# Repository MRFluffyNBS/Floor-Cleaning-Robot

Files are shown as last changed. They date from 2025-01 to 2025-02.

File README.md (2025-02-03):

# Floor-Cleaning-Robot (***Work in Progess***)
This is my attempt during winter break this year at making a (knockoff) Roomba aka a floor-cleaning robot. I wanted to work on a rather simple project over winter break and the topic of a robot vacuum came up when one of my friends suggested the idea. Honestly, I feel like a lot of people have done this before so I primarily did this project just to gain some experience/knowledge. Please keep in mind that this is still a very rough build and there is a lot of stuff I could improve on for this project and also a lot of stuff that I still want to do. I can elaborate on this later, but basically it would have been way better if I actually could get reliable access to a 3d printer... 
As you can see in the following picture of the roomba (I'll be calling it that from now on), a lot of it is being held on with cardboard and tape. 

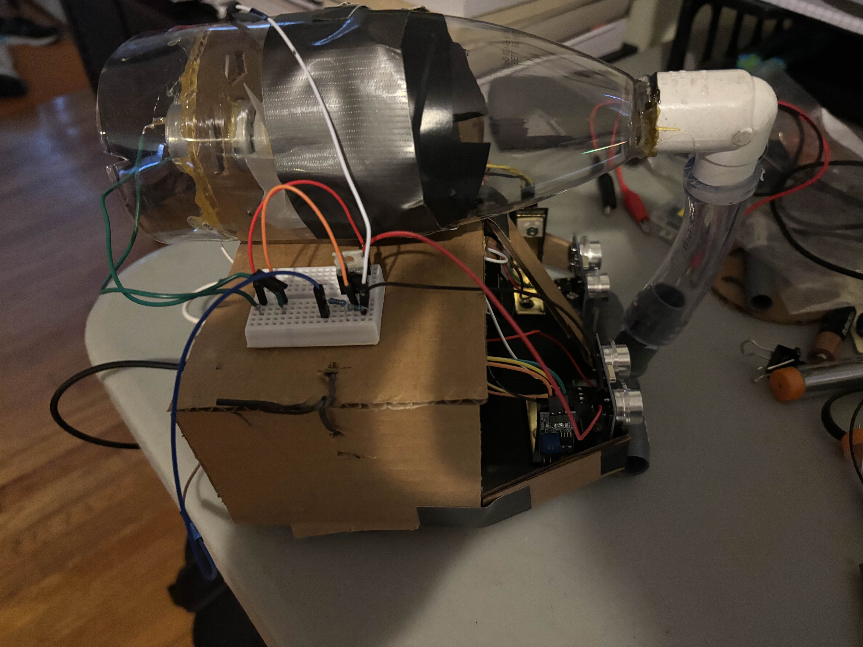
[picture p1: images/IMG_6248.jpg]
Image of completed roomba


### Video demo: 
Iroomba video demo (http://www.youtube.com/watch?v=Y5IRyU6TOsk)

***Click the image above to play video***

Even though the construction may not be the sturdiest, the "roomba" runs well most of the time and is pretty good at obstacle avoidance given that there isn't a carpet or high beam for the robot to get caught on. Once I can use a 3d printer more often, the next goal would be to construct a sleeker and shorter chassis much like a real roomba so that the robot can move around easier. However, the base plate and wheels of the robot are 3d printed, however, there are also parts of the design that I would like to improve on seeing that I could only get stuff 3d printed once at my library. I have also included the CAD files in the repo. Hopefully in the future I can actually get access to a 3D printer :C

## Overview

The microcontroller I am using is an esp32 chip mounted on an Adafruit feather Huzzah32. A normal Arduino uno or most other microcontrollers can be used as well I just used the esp32 because of its wifi features because I also want to implement some web server functionality in the future as well (such as remote control options and updating on status). The motor driver I'm using is a DRV8833 motor driver with two H bridges. It can supply up to 1.5A and I am using two n20 motors geared at about 200 rpm to drive the Roomba wheels. The motor for the vacuum is an RS360 motor and I am just powering that with 6 AA batteries and a MOSFET to turn the vacuum on/off. I am using two HC-SR04 ultrasonic sensors to detect obstacles and two ir proximity sensors to detect if there is a fall off (e.g. the edge of stairs or a table). 

adafruit feather
Adafruit Feather Huzzah ESP32

## Step 1: Chassis + wheels
<p float="left">
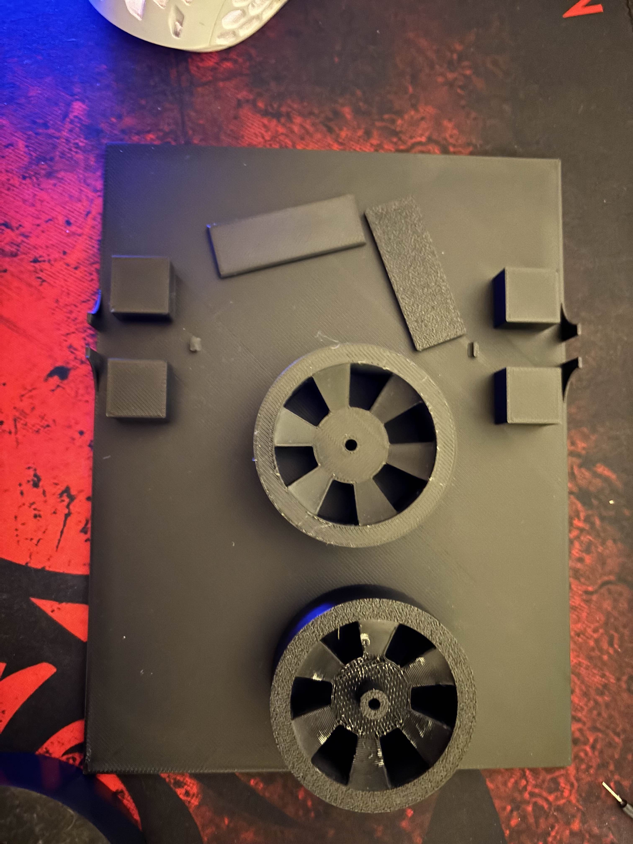
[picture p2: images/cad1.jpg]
Chassis 1
   
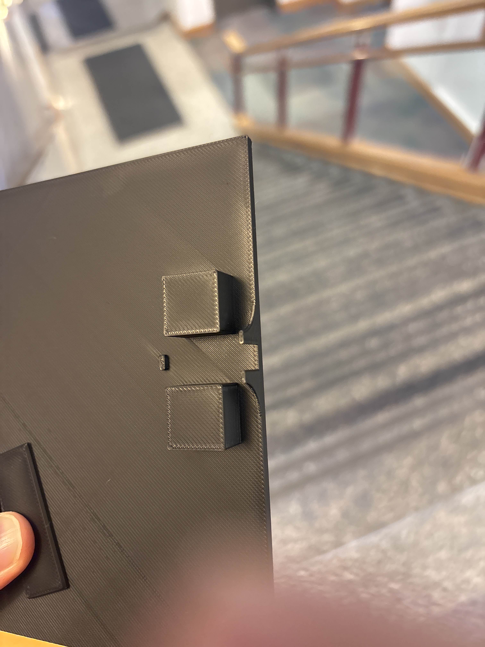
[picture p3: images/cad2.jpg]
Chassis 2
  
</p>

## Step 2: Motor driver + Motors
Chassis 2
In order to control the motor driver, you have to use a H bridge that allows for motors to be run both forward and backward. A H bridge consists of basically 4 transistors. The transistors or switches alternate between npn and pnp resistors, so when a HIGH signal is applied to one side, it turns a switch on and the other switch off. This prevents short circuits and means you only need two inputs to control a h bridge. The motor driver I used had two H bridges so it could control two motors. For each pair of inputs, I connected two GPIO pins on the ESP32. These inputs corresponded to the two wires leading to the motors. To turn the motors on in either direction you just need to set one input pin to HIGH and the other one to LOW. In order to control speed, I made sure all GPIO pins supported PWM. Just use PWM on the input that is normally set HIGH to control the motor speed. 

## Step 3: Sensors 
Sensors intial
For sensors, I used two ultrasonic sensors on the front end of the roomba. If a sensor detects an object in front of it, the roomba turns a random angle the other direction. The same logic is applied to the IR sensors but instead, they are there to make sure there is always a solid floor beneath. The ultrasonic sensor works by sending out a pulse that bounces off an object and is then read by the sensor. The code for this is fairly simple and can be easily found online. Just make sure to account for a 0 in the reading because sometimes the sensor times out and doesn't output a valid reading. This could erroneously trigger that an object is detected in front. 

## Step 2: Motor and Sensor Libraries 
To make writing code easier and allow for better integration of the software when writing a pathfinding algorithm/future setting up for remote use, I made separate classes for turning the motors and object detection for both the ultrasonic sensors and IR proximity sensors. Using these classes, I could create simple functions such as forward/reverse to move the Roomba and also one single command to check if there is an object in front of the sensors. I wrote these classes a separate file in the format of Arduino libraries. They are split into two files each with a .h file for method/class prototypes and a .cpp file for the actual implementation. This [video](https://www.youtube.com/watch?v=IiZl3p-ZohM) goes into it in more detail. 

## Step 5: Powering the Roomba 
Initially I was powering the board, sensors and motors from one LiPo battery. I switched that to a small portable usb charger but there were still problems. One of the biggest problems I had when getting the Roomba to work was the unreliability of the sensors when the motors were under load. When the robot was moving under its own weight, many times it would run into a wall without the sensors triggering. After testing through the serial monitor, I realized that the motors might have been causing a bunch of noise in the system when under load because it would need to draw more power from my power source. After doing some research, I realized that motors were very prone to causing electrical noise and thus needed either capacitors to smooth the voltage or be run off a separate power source. I decided to use a separate power source because it seemed simpler to do so and also because I realized drawing power from two separate usb outputs on the portable charger basically mimicked two separate power sources. As long as you connect the grounds together, the digital logic of the microcontroller will be able to control the motors. 

## Step 6: Vacuum 
For the vacuum, instead of a 5v usb charger, I used 6 AA batteries that would provide 9 volts to the r360 dc motor. This motor draws about 0.8A and could probably be overclocked to 12 volts for a more powerfult vacuum. To turn the vacuum motor on/off, I used a MOSFET to create a relay that could be controlled by the microcontroller. The battery and motor would be connected through the source and drain pins with a 100k resistor between the gate and drain pins to prevent built-up charge in the transistor. A GPIO pin would be connected to the gate with the grounds of the microcontroller and transistor also tied together. In terms of the actual vacuum, I cut a circle of plastic into 8 slices and then used heat to help mold it into a crude fan. I then stuck it onto the motor and used a plastic bottle as the casing with a vegetable mesh between the fan blades and opening. Mostly, my designed was adapted off this [tutorial](https://www.instructables.com/How-to-Make-a-Powerful-Vacuum-Cleaner/). 

## Step 7: Putting everything together 
Sensors intial
Screws were used to mount L brackets and the IR sensors to the front. The ultrasonic sensors also came with screw-mounted brackets. The motors were screwed on with the 3d printed fittings and I also added electrical tape to the wheels for better traction. The breadboard with the esp32 and motor driver were taped on top of the portable charger bank which was then mounted on the back of the roomba. Also I glued the hump piece to the front underside of the roomba so it would stand level. Make sure that most of the weight is right above the wheel axles and not the front hump or else there will be too much friction. Lastly, since I didn't have the time and also the means of using a 3d printer, I just used plain cardboard to create a mount that would hold the vacuum bottle in place along with its relay circuit. In the future, I would like to create a better 3d printed bracket that is not so bulky and also 3d print a better casing for the vacuum. Lastly, I coded in a while loop that would trigger until a button was pressed so that the roomba wouldn't automatically start until I wanted it to. 

## Extra + TODO: Wireless Controlling with ESP32
In the future, other than making a more sleek and compact build that is more 3d printed than cardboard, I also want to integrate the esp32 wifi feature into my project. Right now, I have a remote test folder that contains code that allows me to control the roomba like a rc car. Im hoping to be able to have the roomba give updates onto a html webserver and be able to have a toggle for manual control and automatic control. I always want to be able to turn on and off the vacuum motor itself remotely. Right now, I need to figure out a way to upload the html code onto the webserver in a way where there isnt any lag or any sort of delay because during testing I found that there was often a delay between pressing a button on the website and the roomba actually moving.

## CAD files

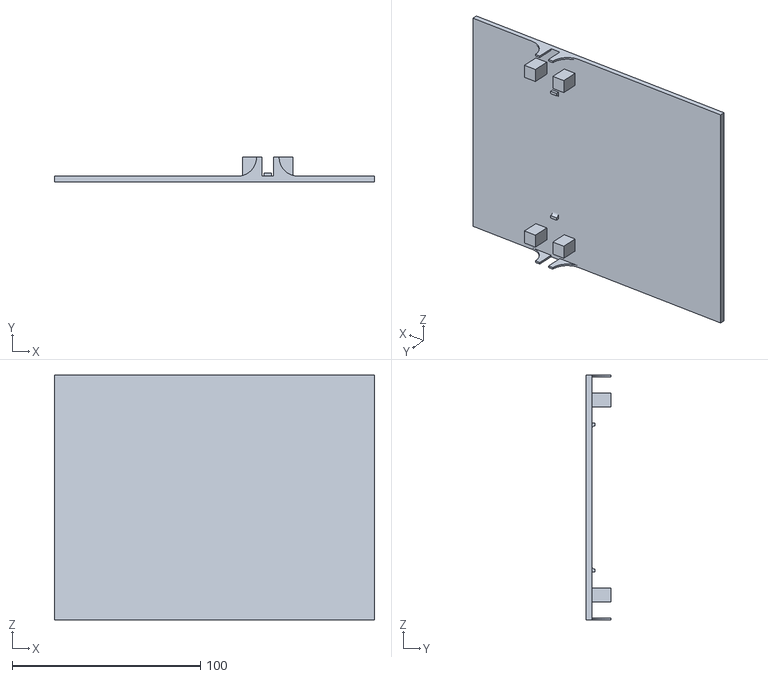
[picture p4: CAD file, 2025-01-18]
baseplate3.STL
170.0 x 13.1 x 130.0

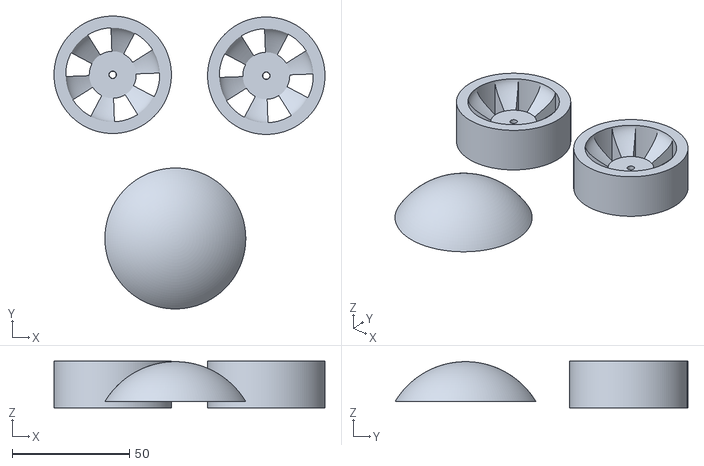
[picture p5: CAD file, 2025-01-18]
wheel+front hump.stl
115.4 x 124.7 x 20.0

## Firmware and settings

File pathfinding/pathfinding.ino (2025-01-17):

#include "roomba_motors.h"
#include "sensors.h"

//right motor pin1 and pin2
const int motor_pin1 = 16;
const int motor_pin2 = 17;
//left motor pin3 and pin4 
const int motor_pin3 = 27;
const int motor_pin4 = 33; 
//duration and speed settings
const int duration = -1; //set the duration to -1 for the motors to turn continously until method stop() is called
int speed = 150;
//Motors initalize
Motors roomba(motor_pin1, motor_pin2, motor_pin3, motor_pin4, speed);

const int rtrig_pin = 18;
const int recho_pin = 5;

const int ltrig_pin = 32;
const int lecho_pin = 15;

const int sensor_tolerance = 15;

Ultson rightSonic(rtrig_pin, recho_pin, sensor_tolerance);
Ultson leftSonic(ltrig_pin, lecho_pin, sensor_tolerance);

const int rir_pin = 4;
const int lir_pin = 14; 

Irsensor rIr(rir_pin);
Irsensor lIr(lir_pin);

const int button_pin = 19;

int degrees = 90;
int direction = 0;

const int switch_pin = 12;

void setup() {
  // put your setup code here, to run once:
  Serial.begin(115200);
  //set pimode for motors
  roomba.begin();
  roomba.printMotors();
  //set pinmode for the ultrasonic sensors
  rightSonic.begin();
  leftSonic.begin();

  rIr.begin();
  lIr.begin();
  
  pinMode(button_pin, INPUT);
  pinMode(13, OUTPUT);
  //set random seed to arbitrary number 
  randomSeed(12346);
  //setting up pinmode for GPIO pin that switches on/off the vacuum
  pinMode(switch_pin, OUTPUT);
  digitalWrite(switch_pin, LOW); //ensures the vacuum is turned off before the roomba starts working
  Serial.println("Off, waiting for signal...");

  while (digitalRead(button_pin) == LOW) { //waits for button to be pressed to turn on
  }

  Serial.println(" Turning on...");
  digitalWrite(switch_pin, HIGH); //turn on high (temp)
}

void loop() {
  //check if the right ultrasonic sensor detects an object first
  
  if (rightSonic.objectDetected() == true || rIr.checkDistance() == true) {
    Serial.println("Right sensor detected");
    roomba.stop();
    delay(100);//Gives the motors time to wind down 
    //Somtimes the only one motor spins up when going directly into reverse
    roomba.reverse(800);

    roomba.stop();
    degrees = random(45, 136); // random number from 45 to 135 degrees
    float time = degrees * (400.0 / roomba.getSpeed());
    //Serial.print("Degrees/time of rotation: "); 
    //Serial.println(time);
    //Turns opposite direction to which sensor has detected an object
    //most likely there is more space on the left if the right sensor detects somehting first
    roomba.left(time);
    delay(60);
    roomba.forward();
  }
  else if (leftSonic.objectDetected() == true || lIr.checkDistance() == true) {
    Serial.println("Left sensor detected");
    roomba.stop();
    delay(100); //Gives the motors time to wind down 
    //Somtimes the only one motor spins up when going directly into reverse
    roomba.reverse(800);

    roomba.stop();
    degrees = random(60, 181); // random number from 45 to 180 degrees
    float time = degrees * 5.0;
    //Serial.print("Degrees/time of rotation: "); 
    //Serial.println(time);
    //same reteoric as the other sensor
    roomba.right(time);
    delay(60);
    roomba.forward();
  }
    else {//proceed forward
    //delay(60);
    roomba.forward();
    }
}

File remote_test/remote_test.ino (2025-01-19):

/*
Testing for remote controlling a car through wifi. Adapted from code from a tutorial from randomnerdtutorials.com
Nathaniel Su 1/4/2025


// Load Wi-Fi library
#include <WiFi.h>
#include "roomba_motors.h"
#include <WebServer.h>

//right motor pin1 and pin2
const int motor_pin1 = 16;
const int motor_pin2 = 17;
//left motor pin3 and pin4 
const int motor_pin3 = 27;
const int motor_pin4 = 33; 
//duration and speed settings
const int duration = -1; //set the duration to -1 for the motors to turn continously until method stop() is called
int speed = 255;
//Motors initalize
Motors roomba(motor_pin1, motor_pin2, motor_pin3, motor_pin4, speed);

// Replace with your network credentials
const char* ssid = "Feather-esp32-Roomba";
const char* password = "123456789";

// Set web server port number to 80
WiFiServer server(80);

// Variable to store the HTTP request
String header;

// Auxiliar variables to store the current output state
String output26State = "off";
String output27State = "off";

// Current time
unsigned long currentTime = millis();
// Previous time
unsigned long previousTime = 0; 
// Define timeout time in milliseconds (example: 2000ms = 2s)
const long timeoutTime = 2000;

void setup() {
  Serial.begin(115200);
  //Initialize motors first 
  roomba.begin();
  roomba.printMotors();

  // Connect to Wi-Fi network with SSID and password
   // Connect to Wi-Fi network with SSID and password
  Serial.println("Setting AP (Access Point)…");
  // Remove the password parameter, if you want the AP (Access Point) to be open
  WiFi.softAP(ssid, password);

  IPAddress IP = WiFi.softAPIP();
  Serial.print("AP IP address: ");
  Serial.println(IP);
  
  server.begin();
}

void loop(){
  WiFiClient client = server.available();   // Listen for incoming clients

  if (client) {                             // If a new client connects,
    currentTime = millis();
    previousTime = currentTime;

    Serial.println("New Client.");          // print a message out in the serial port
    String currentLine = "";                // make a String to hold incoming data from the client
    while (client.connected() && currentTime - previousTime <= timeoutTime) {  // loop while the client's connected
      currentTime = millis();
      if (client.available()) {             // if there's bytes to read from the client,
        char c = client.read();             // read a byte, then
        Serial.write(c);                    // print it out the serial monitor
        header += c;
        if (c == '\n') {                    // if the byte is a newline character
          // if the current line is blank, you got two newline characters in a row.
          // that's the end of the client HTTP request, so send a response:
          if (currentLine.length() == 0) {
            // HTTP headers always start with a response code (e.g. HTTP/1.1 200 OK)
            // and a content-type so the client knows what's coming, then a blank line:
            client.println("HTTP/1.1 200 OK");
            client.println("Content-type:text/html");
            client.println("Connection: close");
            client.println();
            
            // turns the GPIOs on and off
            if (header.indexOf("GET /26/on") >= 0) {
              Serial.println("GPIO 26 on");
              output26State = "on";
              roomba.forward();
            } 
            else if (header.indexOf("GET /26/off") >= 0) {
              Serial.println("GPIO 26 off");
              output26State = "off";
              roomba.stop();
            } 
            else if (header.indexOf("GET /27/on") >= 0) {
              Serial.println("GPIO 27 on");
              output27State = "on";
              roomba.reverse();
            } 
            else if (header.indexOf("GET /27/off") >= 0) {
              Serial.println("GPIO 27 off");
              output27State = "off";
              roomba.stop();
            }
            
            // Display the HTML web page
            client.println("<!DOCTYPE html><html>");
            client.println("<head><meta name=\"viewport\" content=\"width=device-width, initial-scale=1\">");
            client.println("<link rel=\"icon\" href=\"data:,\">");
            // CSS to style the on/off buttons 
            // Feel free to change the background-color and font-size attributes to fit your preferences
            client.println("<style>html { font-family: Helvetica; display: inline-block; margin: 0px auto; text-align: center;}");
            client.println(".button { background-color: #4CAF50; border: none; color: white; padding: 16px 40px;");
            client.println("text-decoration: none; font-size: 30px; margin: 2px; cursor: pointer;}");
            client.println(".button2 {background-color: #555555;}</style></head>");
            
            // Web Page Heading
            client.println("<body><h1>ESP32 Web Server</h1>");
            
            // Display current state, and ON/OFF buttons for GPIO 26  
            client.println("<p>GPIO 26 - State " + output26State + "</p>");
            // If the output26State is off, it displays the ON button       
            if (output26State=="off") {
              client.println("<p><a href=\"/26/on\"><button class=\"button\">ON</button></a></p>");
            } 
            else {
              client.println("<p><a href=\"/26/off\"><button class=\"button button2\">OFF</button></a></p>");
            } 
               
            // Display current state, and ON/OFF buttons for GPIO 27  
            client.println("<p>GPIO 27 - State " + output27State + "</p>");
            // If the output27State is off, it displays the ON button       
            if (output27State=="off") {
              client.println("<p><a href=\"/27/on\"><button class=\"button\">ON</button></a></p>");
            } 
            else {
              client.println("<p><a href=\"/27/off\"><button class=\"button button2\">OFF</button></a></p>");
            }
            client.println("</body></html>");
            
            // The HTTP response ends with another blank line
            client.println();
            // Break out of the while loop
            break;
          } else { // if you got a newline, then clear currentLine
            currentLine = "";
          }
        } else if (c != '\r') {  // if you got anything else but a carriage return character,
          currentLine += c;      // add it to the end of the currentLine
        }
      }
    }
    // Clear the header variable
    header = "";
    // Close the connection
    client.stop();
    Serial.println("Client disconnected.");
    Serial.println("");
  }
}*/
